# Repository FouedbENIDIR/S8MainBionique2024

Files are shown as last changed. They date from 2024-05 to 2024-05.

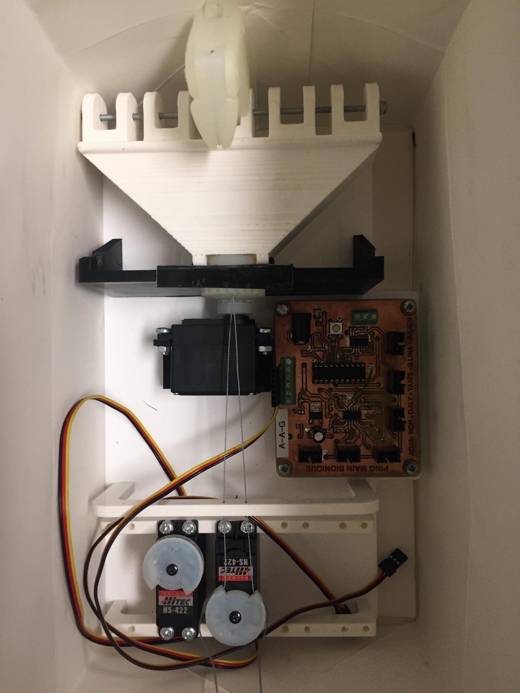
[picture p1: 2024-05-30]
Prototype final.jpeg

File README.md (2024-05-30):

#S8MainBionique2024
Ce répertoire est un recueil des travaux effectués durant le projet S8 2024.

Ce projet, initié il y a quelques années, a pour but de concevoir une main mécanique contrôlée électroniquement par les signaux électriques que le corps envoie au niveau d'un moignon issu d'un bras amputé.

Notre projet S8, après de nombreux problèmes notamment au niveau du code du MSP et de la carte, a été guidé par le désir d'avancer sur la partie mécanique.
Beaucoup de design ont été produit auparavent mais aucun n'est viable et utilisable. En effet la problématique du doigt ayant un pli naturelle a été étudié et plusieurs résultats disponible dans le fichier V2_documentation Mécanique sont indiqués.

DOCUMENT TRES IMPORTANT A LIRE ET A COMPRENDRE AVANT D'AVANCER DANS LE PROJET PARTIE MECANIQUE.

Plusieurs prototypes ont été conçus en répondant aux critères nécessaires énumérés dans le rapport mécanique, présent dans ce répertoire.
"L'utilisation d'une main à 3-4 doigts, avec 2 servomoteurs par doigt, ainsi que l'utilisation de roulements pour fluidifier le mouvement entre chaque phalange doit être étudiée autour d'un projet S8 complet, avec une partie de réflexion autour de nos conclusions, une partie de conception à partir de nos propositions de modèles et une partie de tests permettant de valider ou non le modèle proposé. Si les tests ne sont pas concluants, le groupe reviendra à la conception."

Un projet répondant aux cahier des charges techniques et aux défis encourus peut être un bon moyen de produire une main viable embarquant les servomoteurs mais aussi la batterie.

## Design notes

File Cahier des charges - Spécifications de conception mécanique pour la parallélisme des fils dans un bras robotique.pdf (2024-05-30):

ILINA.K | Date: 08/12/2023
| DOCUMENT TECHNIQIUE : PARTIE MECANIQUE de la main bionique (version 3)
Auteur | Durée de travail
ILINA KHIAT | 12 H
| ➢ Dimanche 26/11/2023 : Rédaction de la
| traçabilité des exigences techniques de la conception mécanique (2H) ➢ Dimanche 03/12/2023 : Continuer la
| Traçabilité des exigences techniques de la conception mécanique (2H) ➢ Jeudi 07/12/2023 : Utilisation du logiciel
| de conception SolidWorks + Rédaction d'une section détaillée décrivant les corrections techniques à apporter lors du processus de conception (3H) ➢ Vendredi 08/12/2023 : Finaliser le cahier des charges + Compléter le Document Principal des Binômes + publier le cahier des charges sur le groupe Teams (5H)

Cahier des charges : conception mécanique

## SPÉCIFICATIONS DE CONCEPTION MÉCANIQUE POUR LE PARALLÉLISME DES FILS DANS UN BRAS

## ROBOTIQUE

Introduction

L'objectif de ce document est de définir les spécifications mécaniques cruciales et les principes nécessaires pour atteindre un parallélisme optimal des fils au niveau des articulations d'un bras robotique pendant les mouvements d'articulation. Les écarts par rapport au parallélisme peuvent entraîner une augmentation des tensions mécaniques dans les tendons, une manœuvrabilité réduite des articulations des doigts et des problèmes potentiels d'enchevêtrement des fils lors de mouvements répétés, ce qui affecte la fonctionnalité globale du bras, sa précision et la durée de vie attendue. Maintenir le parallélisme des fils est une considération importante pour les ingénieurs concepteurs de bras robotiques.

Objectif

L'objectif principal de ce document technique est de définir clairement les spécifications de conception mécanique et les tolérances nécessaires pour concevoir un système de bras robotique qui maintient de manière fiable le parallélisme des fils à chaque articulation pendant les mouvements d'articulation.

Exigences de conception mécanique

La section suivante décrit les principales exigences de conception mécanique à suivre pour garantir que les tendons entre chaque articulation maintiennent un parallélisme adéquat pendant les mouvements d'ouverture et de fermeture de l'articulation.

1. Alignement du Parallélisme des Fils : Les tendons au-dessus et en dessous de chaque articulation doivent être conçus pour maintenir un parallélisme tangentiel lors de l'articulation. Un serrage strict sera nécessaire pendant la phase de conception mécanique.
2. Propriétés du Fil du Tendon : Les tendons doivent être construits avec un fil de haute résistance présentant une élongation élastique minimale sous des charges de tension.
3. Flexibilité du Fil du Tendon : Le matériau du tendon doit permettre un pliage fluide autour d'un rayon minimum de 3 mm sans pliage ni flambage lorsque l'articulation se déplace.
4. Routage Correct des Tendons : Les canaux utilisés pour acheminer les tendons à travers chaque articulation doivent être conçus avec précision pour maintenir une séparation constante des fils et éviter le chevauchement ou l'enchevêtrement pendant le mouvement de l'articulation.
5. Méthode d'Actionnement : Il est recommandé que les mouvements des doigts soient actionnés à l'aide de quatre moteurs servo haute précision de 10g ,4.2 - 6 V pour fournir le couple et le contrôle de position nécessaires pour un mouvement répétable des tendons parallèles.

6. Capacité de Charge : La main robotique devrait pouvoir supporter une masse d'au moins 100 g.
7. Poids : La conception et le matériau devraient donner une structure légère de moins de 300 g.
8. Manipulation d'Objets : Être capable de manipuler des objets couramment utilisés de taille 50 à 100 mm, tels que la manipulation d'objets d'usage quotidien.

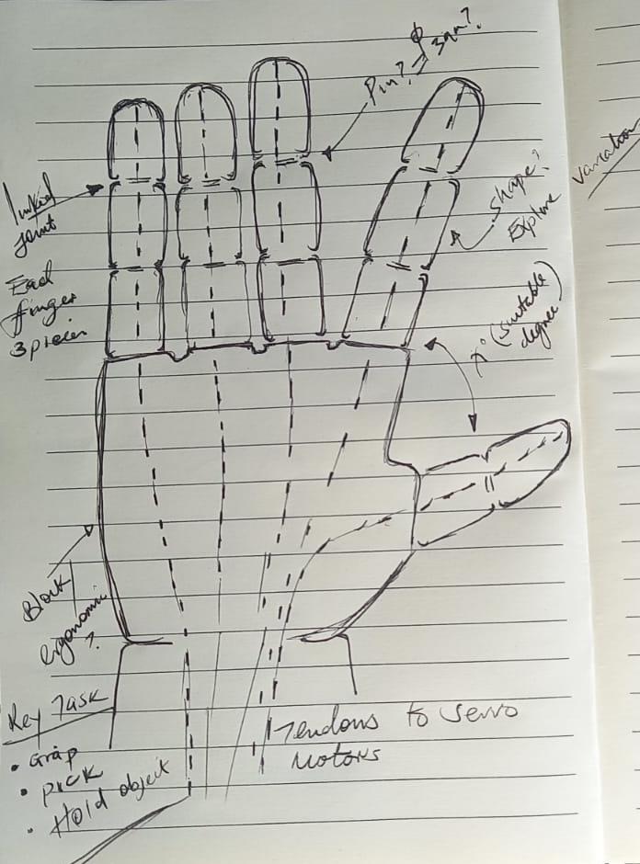
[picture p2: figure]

Figure 1.Croquis préliminaire des principales parties et fonctionnalités du bras.

PARALLÉLISME DES FILS DANS LE MODÈLE "RobHand".

Correction du Parallélisme des Fils.

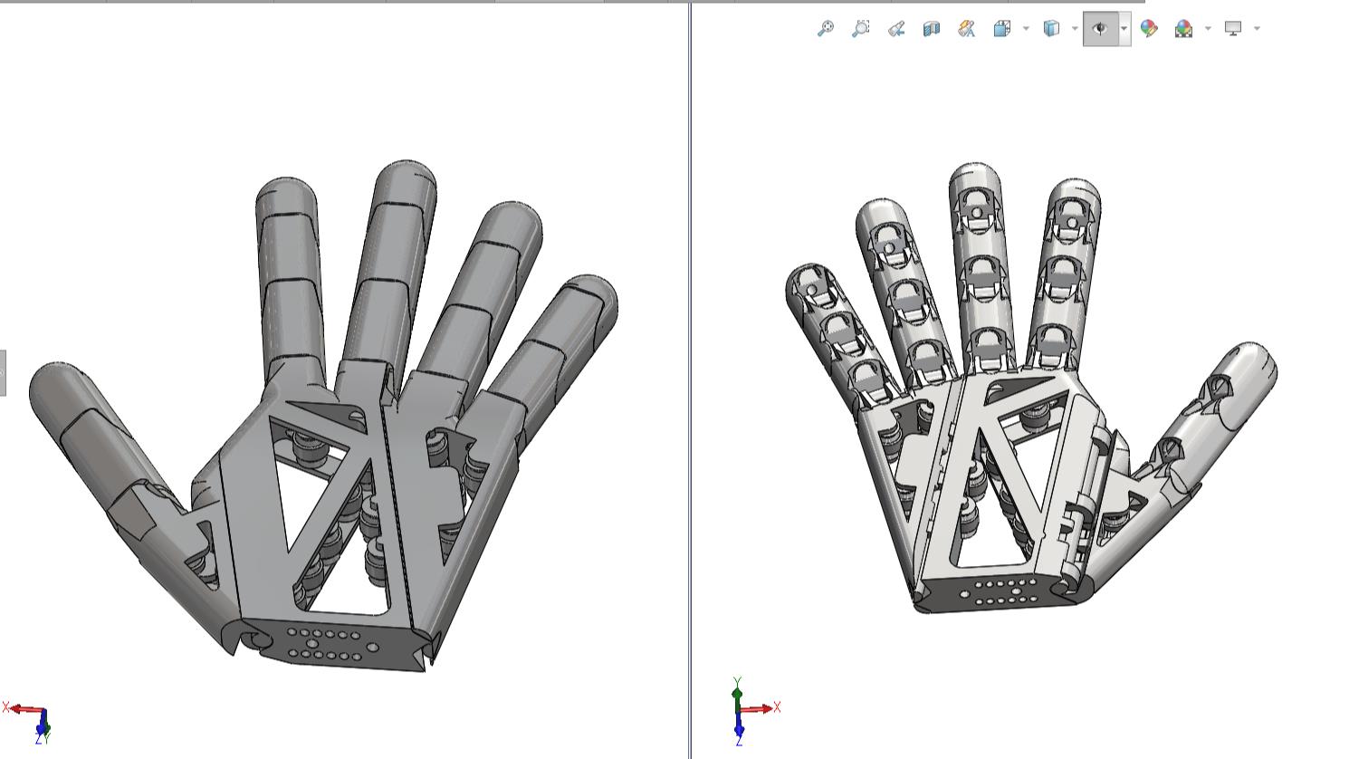
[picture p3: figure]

Figure 2.Capture d'écran du modèle CAO 3D du "RobHand" montrant la vue supérieure et intérieure de la main bionique

À partir du modèle CAO fourni, les fils des tendons au-dessus et en dessous des articulations ne sont pas parallèles lorsque les articulations sont en mouvement, comme illustré dans les images ci-dessous.

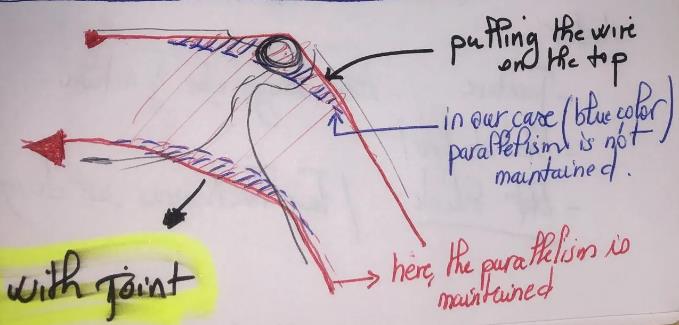
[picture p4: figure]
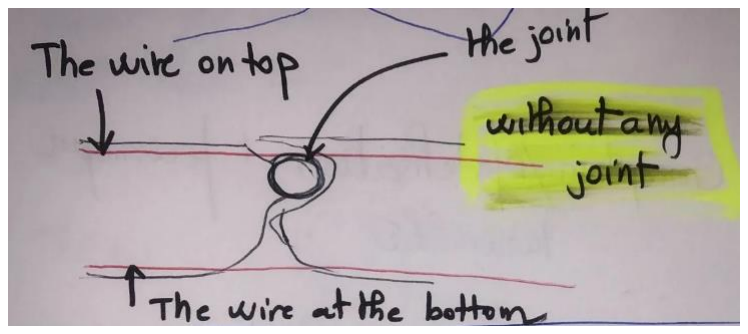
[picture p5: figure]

Figure 3.À droite, articulation d'échantillon en position ouverte. À gauche, articulation d'échantillon montrant un écart de parallélisme.
La procédure de correction de ce modèle impliquera les étapes suivantes :
1. Inspecter le modèle 3D pour identifier comment les sections articulaires spécifiques ont été modélisées.

2. Analyser les trajets de fil existants pour comprendre comment différents paramètres affectent le parallélisme des fils pendant l'articulation.
3. Modifier les angles des articulations et les trajets des fils dans le modèle 3D pour créer un chemin de fil plus lisse et plus parallèle.
4. Utiliser un logiciel de simulation pour visualiser le mouvement des fils pendant l'articulation.
5. Imprimer en 3D une articulation d'échantillon pour tester et itérer en conséquence.

Observations

Une coupe transversale d'un doigt montre que :

- Il y a un routage correct des fils qui garantit qu'il n'y a pas d'enchevêtrement pendant l'articulation.
- Le diamètre maximal autorisé du fil est de 3 mm, mais les chemins le long des doigts ont un espace allant jusqu'à 4,2 mm.
- Le trajet du canal au-dessus de l'articulation du doigt permet au fil du tendon de s'enrouler autour de l'articulation du doigt lorsqu'il se ferme.

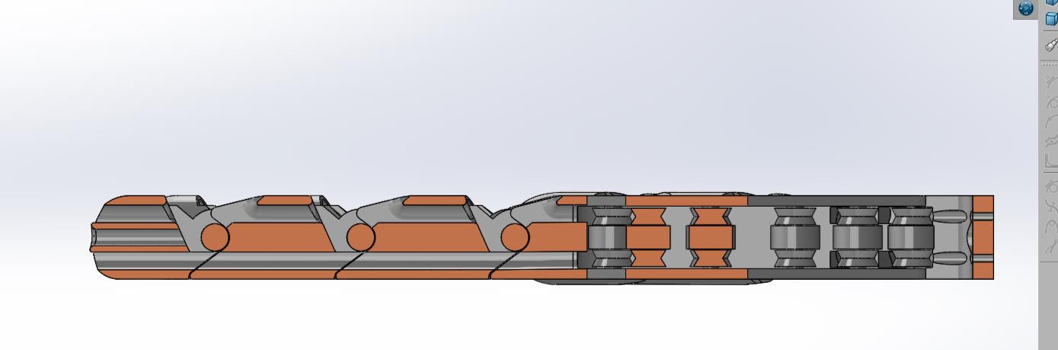
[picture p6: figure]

Figure 4.Vue en coupe d'un doigt et de la paume.
- En analysant le côté intérieur du doigt, on observe que le côté avant des phalanges intermédiaires, des phalanges proximales et de la section des articulations a un écart d'environ ≈ 10 mm par rapport à l'axe de l'articulation. C'est à ce point que le fil du tendon perd son parallélisme.

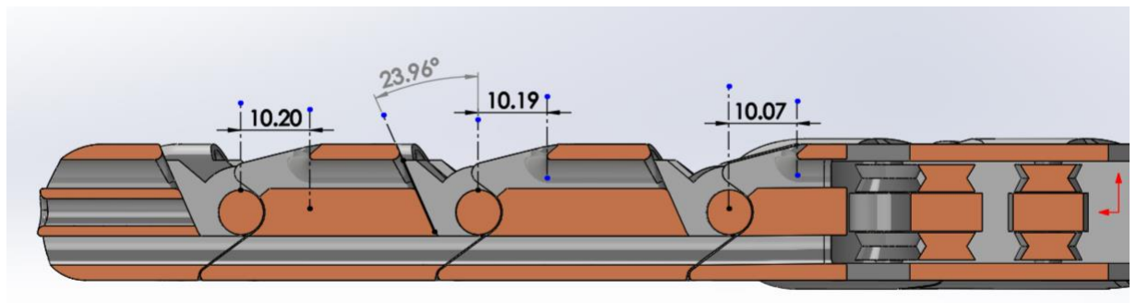
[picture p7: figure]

Figure 5.Décalages de mesure par rapport à l'axe de rotation de l'articulation
- Une inspection minutieuse montre le chemin possible emprunté par le tendon lorsqu'il est tiré.

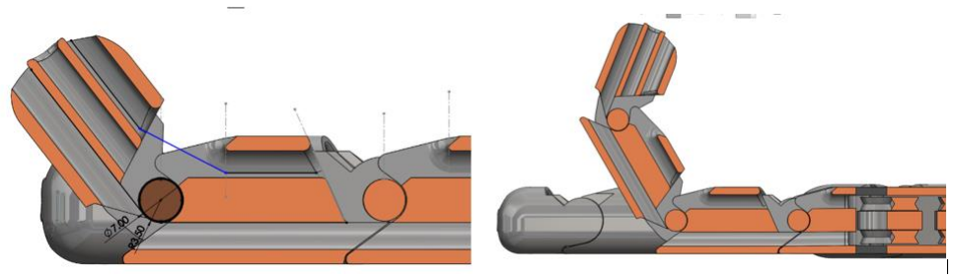
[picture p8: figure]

Figure 6.Différences de flexion des niveaux du doigt d'échantillon.

Ajustements nécessaires

Pour corriger le parallélisme, les phalanges intermédiaires, les phalanges proximales et les points d'articulation seront ajustés par rapport à l'axe de l'articulation afin de maintenir un parallélisme quasi tangentiel entre les tendons supérieur et inférieur.

Calculs mécaniques

Force dans le doigt.

La résistance théorique du doigt, lorsqu'il est complètement ouvert, peut être calculée en analysant les moments créés autour de chaque articulation dans le doigt par ;

Moment = Force x Distance perpendiculaire

M = F x d

Cependant, le moment de l'articulation de l'articulation sera le plus grand, car c'est le plus éloigné et il fournit également la force de rotation qui limite la charge que nous pouvons soulever à l'extrémité du doigt.

Quelle est la force de traction dans le tendon ? Cela sera dérivé par la force de rotation maximale du servo, qui est de 10 kg-cm (1N/M).

Ainsi,

F2 = τServo . d

F2 = 1(N/M) x 10mm

F2 = 10N (Tension dans le Tendon)

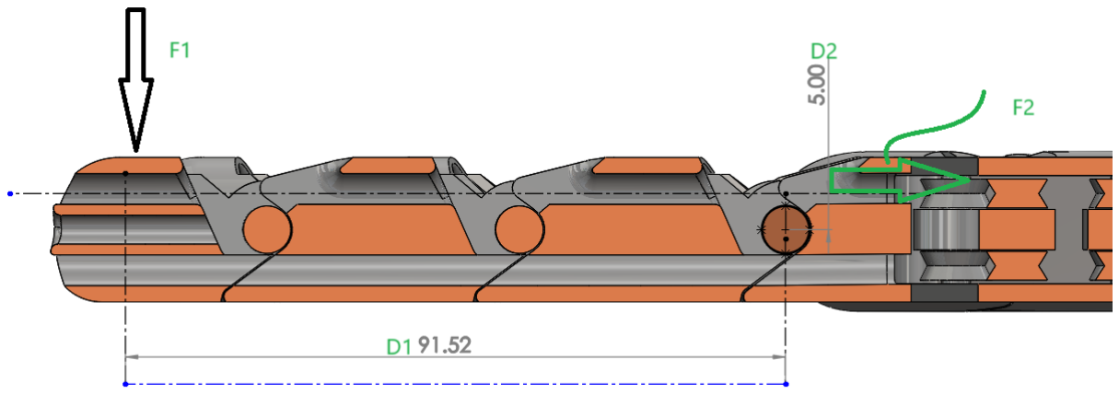
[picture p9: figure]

Figure 7. Forces et distances prises en compte pour les calculs de force.

Ensuite,

F1D1 = F2D2

F1 = (F2D2

)/D1

F1 =

10 x 5
91.52
F1 = 0.55N

Mass 1 ≈ 56.08 g

Cela signifie qu'une force de 0,55N peut être appliquée à chaque doigt lorsqu'il est complètement ouvert. Cependant, lorsque le doigt se replie, le résultat sera un moment moindre autour de l'articulation de l'articulation, et les extrémités appliqueront plus de force à mesure qu'elles se ferment davantage.

Supposons, pendant la flexion, que la distance D 1 = 30 mm, cela permettrait au doigt de supporter environ 163 g, ce qui donnerait une capacité de levage totale du RoboHand d'environ 652 g.

La préℎension maximale de l

′extrémité du doigt ≈ 163g par doigt

Vitesse d'actionnement du doigt

Supposons que notre servo ait une vitesse de fonctionnement de 0,15 s/60⁰. Une rotation complète du poignet d'une position paume vers le haut à une position paume vers le bas (180⁰).

Par conséquent, cela prend (0,15/60) *180 = 0,45 s.

Supposons qu'un tendon se déplace d'environ 2 cm pour déplacer le doigt de complètement ouvert à complètement fléchi.

En utilisant la formule de longueur d'arc

Longueur =

n

0
360⁰ x 2πr

Où la longueur est de 2 cm, r est le rayon des cornes de servo personnalisées (7 mm)

Nous constatons que le servo doit tourner de 160⁰ pour ouvrir/fermer complètement chaque doigt. Cela donne le temps maximal pour ouvrir/fermer un doigt comme (0,15/60) *160 = 0,4 s.

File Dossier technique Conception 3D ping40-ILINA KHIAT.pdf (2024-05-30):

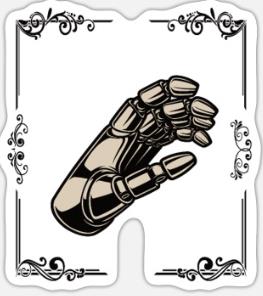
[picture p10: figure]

ILINA KHIAT | Conception mécanique-Prototype de main robotique 2023/2024 | Ping : 40

# DOSSIER TECHNIQUE DE CONCEPTION 3D POUR LE DOIGT ET PROTOTYPE DE MAIN ROBOTIQUE

REALISE PAR : ILINA KHIAT

Introduction.

L'objectif du projet est de concevoir un doigt robotique permettant au fil de tendon de maintenir un parallélisme au sein des phalanges articulaires lors de l'articulation du doigt. Le doigt choisi pour cette conception est le majeur.

CONCEPTION 1

Partie 1. CONCEPTION D'UN SEUL DOIGT ROBOTIQUE

Esquisses de concept

Les esquisses de concept initiales ont été créées en tenant compte des ratios des portions de doigt entre les phalanges distales, intermédiaires et proximales du majeur.

Modélisation 3D

En utilisant SolidWorks, le contour des doigts a été utilisé pour transformer l'esquisse en un modèle 3D détaillé. Cela impliquait l'utilisation des fonctionnalités de SolidWorks telles que les esquisses, les images d'esquisses, les extrusions, les révolutions et les lofts. Un modèle maître à plusieurs corps du doigt a été conçu, servant de base pour les étapes ultérieures de perfectionnement du design.

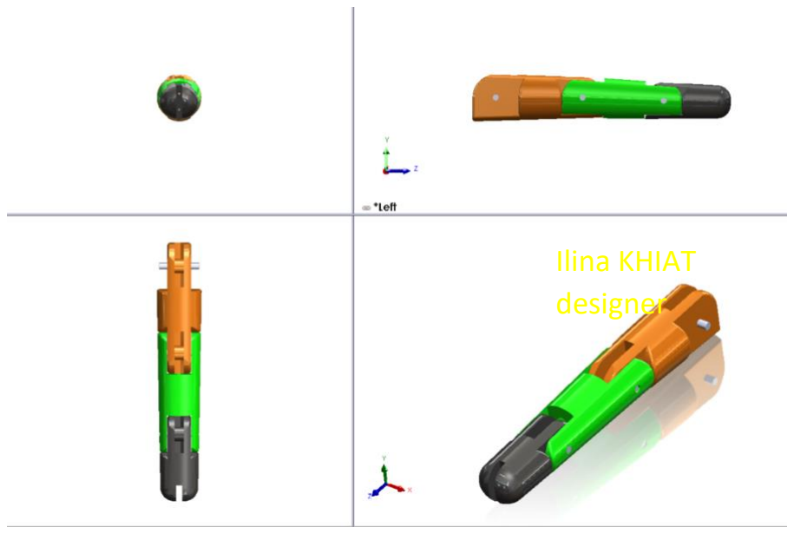
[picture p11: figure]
Ilina KHIAT designer

Figure 2. Vue en première angle du doigt conçu

Pendant le processus de modélisation, une attention particulière a été accordée pour s'assurer que les parties du doigt permettaient au fil de tendon de passer à travers les différentes articulations du doigt tout en maintenant le parallélisme.

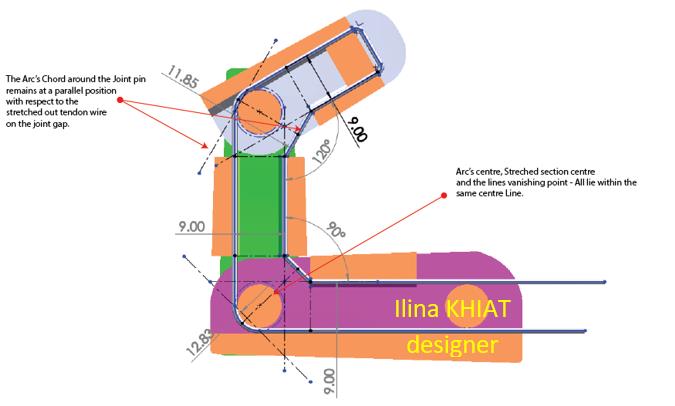
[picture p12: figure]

Figure 3. Vue en coupe du doigt montrant les dimensions pour le parallélisme du tendon.

Assemblage et Simulation

À partir de la partie à plusieurs corps, des parties individuelles des phalanges du doigt ont été créées en utilisant la commande " save body ".

Figure 4. Modèles dérivés des phalanges proximale, intermédiaire, distale et de la broche d'articulation du doigt

Les parties du doigt ont ensuite été importées dans l'environnement d'assemblage de SolidWorks et assemblées à l'aide de liaisons appropriées telles que les liaisons articulées, concentriques, de largeur, coïncidentes et de limitation. Ces liaisons ont permis l'étude du mouvement du doigt.

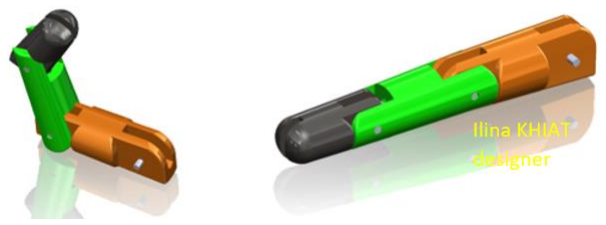
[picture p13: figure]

Figure 5. Assembler le doigt.

Après la création de l'assemblage, une analyse de mouvement avec SolidWorks a été utilisée pour examiner comment les phalanges du doigt s'articulent tout en maintenant le parallélisme requis du fil de tendon autour des points d'articulation.

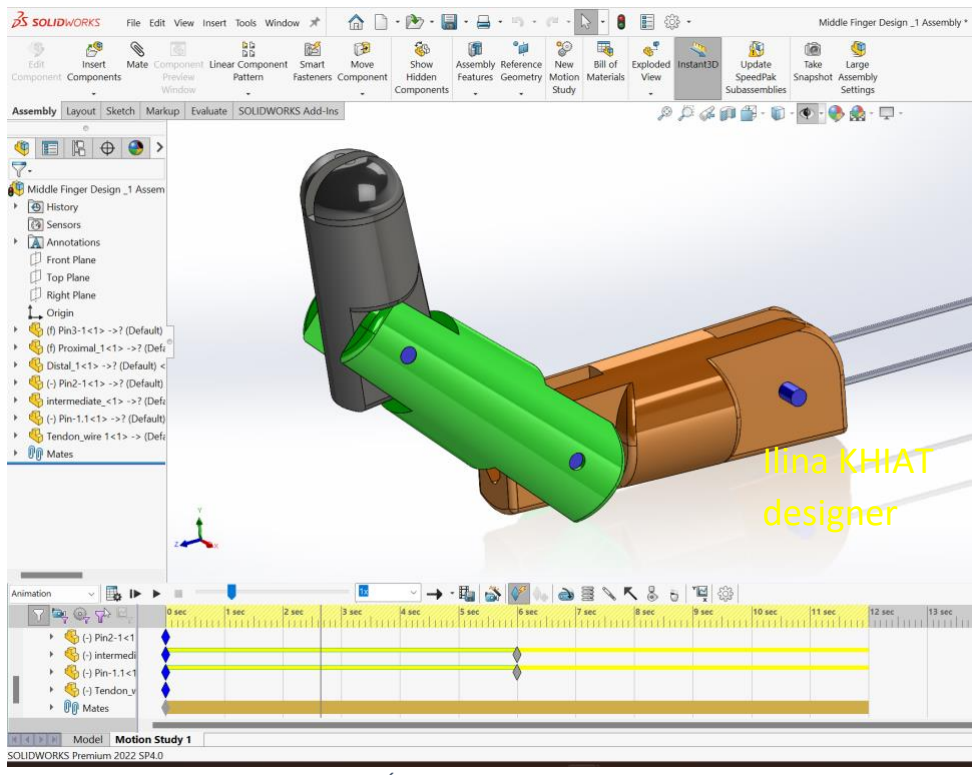
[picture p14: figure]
Ilina KHIAT designer

Figure 6.Étude de mouvement du doigt

Le comportement cinématique d'un assemblage, dans le contexte de SolidWorks, se réfère à la manière dont les composants interagissent et se déplacent les uns par rapport aux autres. Pour examiner le mouvement des fils au niveau des phalanges du doigt, j’ai utilisé l'option "SolidWorks Motion Analysis". Cette fonctionnalité permet de simuler et de suivre le mouvement des composants individuels, comme les fils dans le cas des phalanges du doigt. Comme le montre la configuration en haut, le parallélisme des fils est maintenu pendant l'articulation du doigt. Cela peut être une étape importante pour valider la conception et optimiser le mécanisme du doigt dans le modèle 3D.

Figure 7.Dessin technique de conception d'un doigt robotique 1

CONCEPTION 2

Partie 1. CONCEPTION D'UN SEUL DOIGT ROBOTIQUE

Esquisses de concept

Les esquisses de concept initiales ont été créées en tenant compte des ratios des portions de doigt entre les phalanges distales, intermédiaires et proximales du majeur.

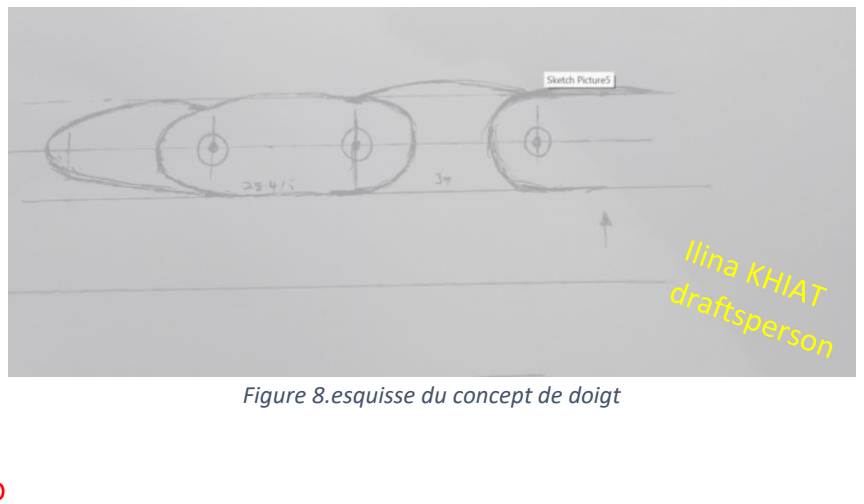
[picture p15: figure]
Figure 8.esquisse du concept de doigt

Modélisation 3D

En utilisant SolidWorks, le contour des doigts a été utilisé pour transformer l'esquisse en un modèle 3D détaillé. Cela impliquait l'utilisation des fonctionnalités de SolidWorks telles que les esquisses, les images d'esquisses, les extrusions, les révolutions et les lofts. Un modèle principal à plusieurs corps du doigt a été conçu, servant de base pour les étapes ultérieures de perfectionnement du design.

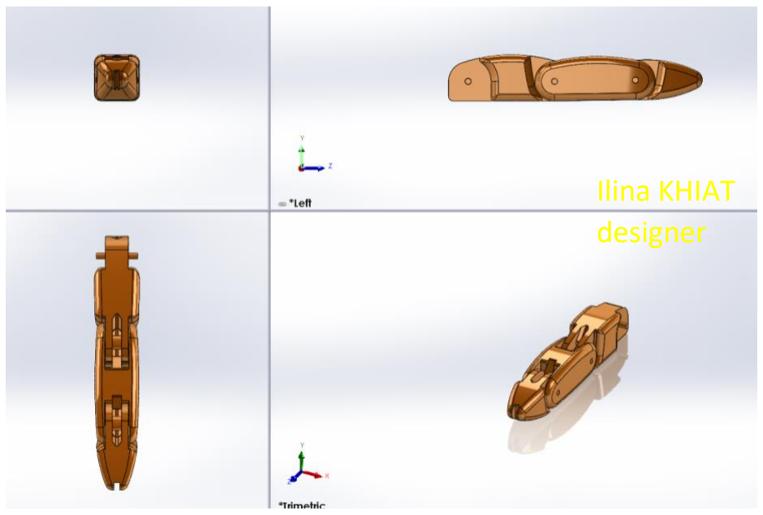
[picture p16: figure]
Ilina KHIAT designer

Figure 9. Vue en première angle du doigt conçu

Pendant le processus de modélisation, une attention particulière a été accordée pour s'assurer que les parties du doigt permettaient au fil de tendon de passer à travers les différentes articulations du doigt tout en maintenant le parallélisme.

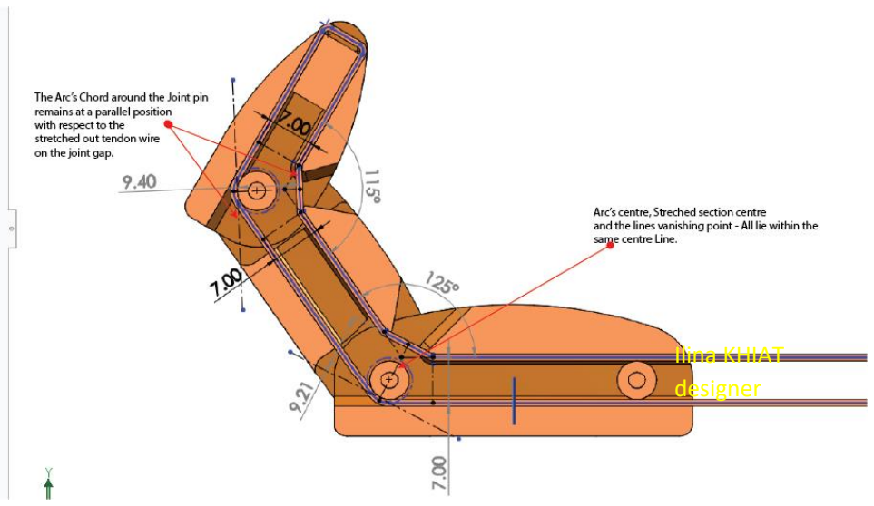
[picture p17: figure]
Ilina KHIAT designer

Figure 10. Vue en coupe du doigt montrant les dimensions pour le parallélisme du tendon.

Assemblage et Simulation

À partir de la partie à plusieurs corps, des parties individuelles des phalanges du doigt ont été créées en utilisant la commande " save body ".

Figure 10. Modèles dérivés des phalanges proximale, intermédiaire, distale et de la broche d'articulation du doigt

Les parties du doigt ont ensuite été importées dans l'environnement d'assemblage de SolidWorks et assemblées à l'aide de liaisons appropriées d’assemblage telles que les liaisons articulées, concentriques, de largeur, coïncidentes et de limitation. Ces liaisons ont permis l'étude du
mouvement du doigt.

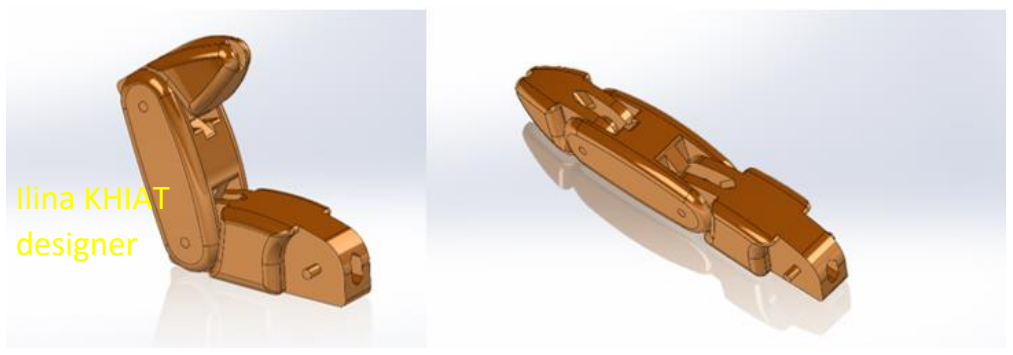
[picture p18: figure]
Ilina KHIAT designer

Figure 11. Assembler le doigt.

Après la création de l'assemblage, une analyse de mouvement avec SolidWorks a été utilisée pour examiner comment les phalanges du doigt s'articulent tout en maintenant le parallélisme requis du fil de tendon autour des points d'articulation.

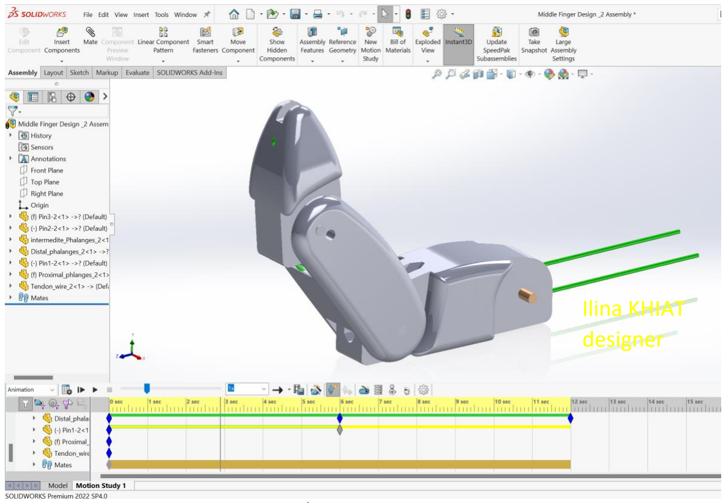
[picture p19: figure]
Ilina KHIAT designer

Figure 12.Étude de mouvement du doigt

Figure 13.Dessin technique de conception d'un doigt robotique 2

CONCEPTION 3

Partie 1. CONCEPTION D'UN SEUL DOIGT ROBOTIQUE

Esquisses de concept

Les esquisses de concept initiales ont été créées en tenant compte des ratios des portions de doigt entre les phalanges distales, intermédiaires et proximales du majeur.

Modélisation 3D

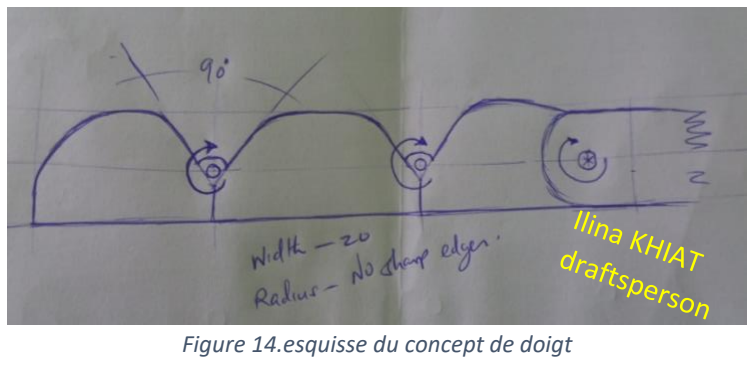
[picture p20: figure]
Figure 14.esquisse du concept de doigt

En utilisant SolidWorks, le contour des doigts a été utilisé pour transformer l'esquisse en un modèle 3D détaillé. Cela impliquait l'utilisation des fonctionnalités de SolidWorks telles que les esquisses, les images d'esquisses, les extrusions, les révolutions et les lofts. Un modèle principal à plusieurs corps du doigt a été conçu, servant de base pour les étapes ultérieures de perfectionnement du design.

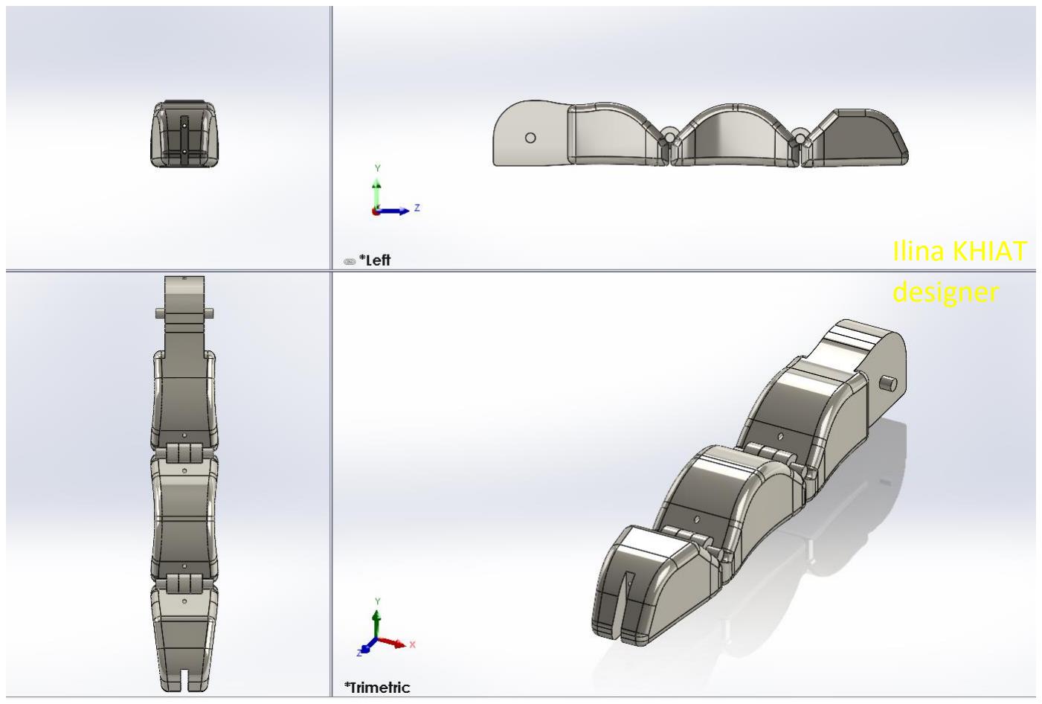
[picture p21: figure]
Ilina KHIAT designer

Figure 15.Vue en première angle du doigt conçu

Pendant le processus de modélisation, une attention particulière a été accordée pour s'assurer que les parties du doigt permettaient au fil de tendon de passer à travers les différentes articulations du doigt tout en maintenant le parallélisme.

Figure 16. Vue en coupe du doigt montrant les dimensions pour le parallélisme du tendon.

Assemblage et Simulation

À partir de la partie à plusieurs corps, des parties individuelles des phalanges du doigt ont été créées en utilisant la commande " save body ".

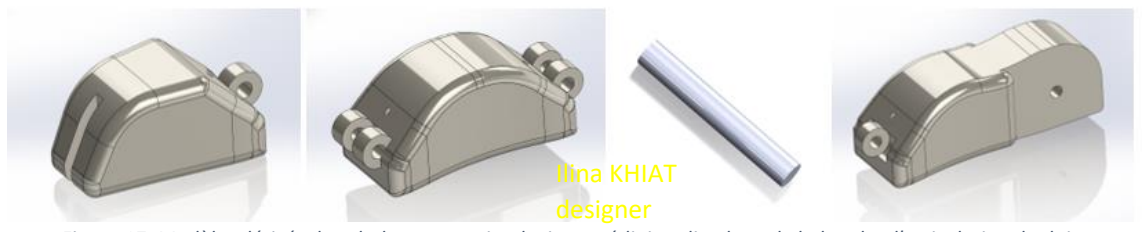
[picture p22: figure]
Ilina KHIAT designer

Figure 17. Modèles dérivés des phalanges proximale, intermédiaire, distale et de la broche d'articulation du doigt

Les parties du doigt ont ensuite été importées dans l'environnement d'assemblage de SolidWorks et assemblées à l'aide de liaisons appropriées d’assemblage telles que les liaisons articulées, concentriques, de largeur, coïncidentes et de limitation. Ces liaisons ont permis l'étude du mouvement du doigt.

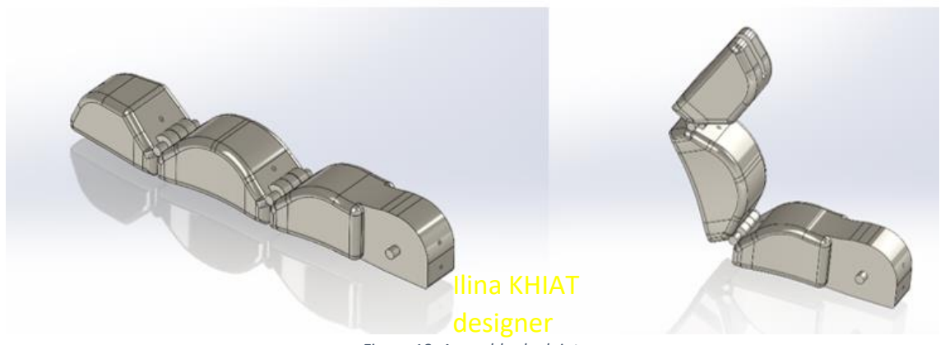
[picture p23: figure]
Ilina KHIAT designer

Figure 18. Assembler le doigt.

Après la création de l'assemblage, une analyse de mouvement avec SolidWorks a été utilisée pour examiner comment les phalanges du doigt s'articulent tout en maintenant le parallélisme requis du fil de tendon autour des points d'articulation.

Figure 19.Étude de mouvement du doigt

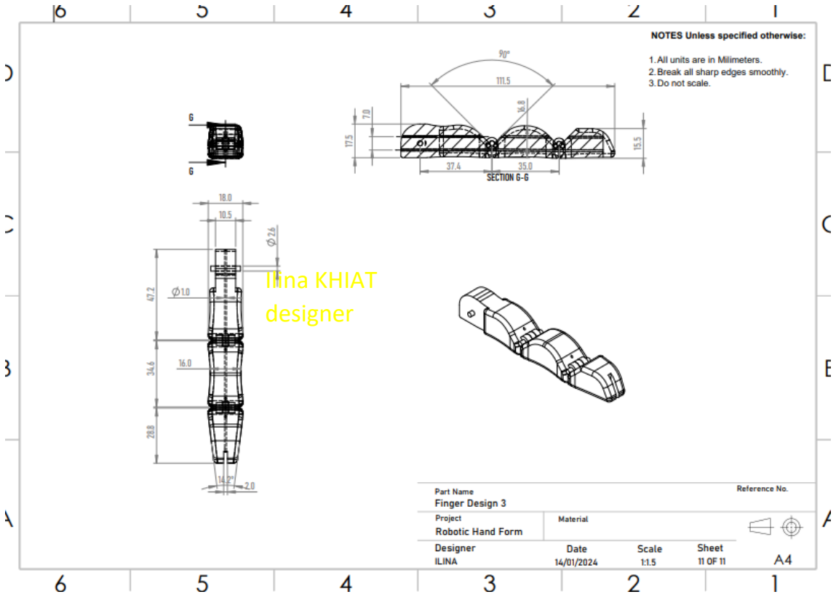
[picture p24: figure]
Ilina KHIAT designer

Figure 20.Dessin technique de conception d'un doigt robotique 3

b. Introduction.

La prochaine phase du projet visait à créer une "main robotique" avec 6 doigts actionnés par 6 servomoteurs, capable d'effectuer un mouvement de supination. La structure du modèle était guidée par le modèle illustré.

Note : Une modification a été apportée après la conception de ces trois prototypes de main

robotique. La modification consistait à supprimer un doigt (le sixième) et à ajuster les trois prototypes déjà conçus avec tous les éléments des maquettes.

Partie 2. CONCEPTION DU PROTYPE DE LA MAIN ROBOTIQUE

Pour comprendre la conception du prototype à réaliser, je me suis basée sur un dessin ci-dessous illustrant l'idée.

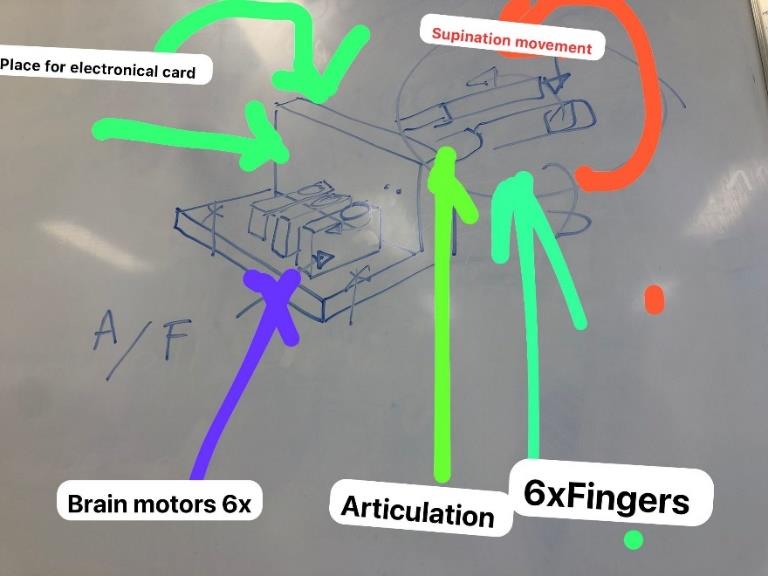
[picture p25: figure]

Figure 21. esquisse du "prototype de main robotique".

Le modèle du servomoteur à utiliser était le servomoteur Deluxe HS-422, avec ses dimensions telles qu'indiquées dans le diagramme ci-dessous.

Figure 22.Datasheet des servomoteurs DELUXE HS-422

Disposition des composants.

En tenant compte du croquis, de la taille du servomoteur et des dimensions des doigts, un plan pour connecter les composants au sein d'une base a été développé en utilisant une esquisse dimensionnée de SolidWorks.

Ilina KHIAT designer

Figure 23.Esquisse de la disposition des composants.

c. Forme du métacarpe

Avec les composants disposés, un modèle 3D détaillé du métacarpe a été conçu pour accueillir les six doigts. La section interne a été évidée pour permettre le passage des fils de tendon et réduire le poids.


Figure 24 : Modèle du métacarpe

La forme métacarpienne est connectée au mécanisme de supination à l'aide d'une vis M3.

d. Engrenages de supination.

Pour permettre le mouvement de supination, des engrenages imprimés en 3D, reliés à un servomoteur, sont conçus et intégrés. Ces engrenages se composent d'un engrenage conducteur avec 11 dents et d'un engrenage mené avec 20 dents.

Figure 25. Engrenages de supination

L'engrenage mené comporte une série de trous à travers lesquels passent les fils de tendon pour éviter tout emmêlement pendant le mouvement.

e. Guide des fils de tendon.

Pour organiser davantage les fils de tendon, un guide vertical avec des trous a été conçu pour garantir que les fils provenant de l'engrenage mené de supination sont sur un plan horizontal plat lorsqu'ils entrent dans les poulies du servomoteur.

Ilina KHIAT designer

Figure 26. Guide des fils de tendon.

f. Poulies de servomoteur.

Connectées aux servomoteurs, les poulies maintiennent les extrémités des fils de tendon au-dessus et en dessous de chaque doigt. Elles facilitent l'articulation des doigts lorsqu'elles sont actionnées par les servomoteurs, soit en tirant, soit en relâchant les fils de tendon.

Figure 27.Poulies de servomoteur.
g. Supports de servomoteur.

Les supports de servomoteur sont également conçus pour permettre aux moteurs d'être fixés par une vis M4.

Figure 28.Supports de servomoteurs h. Base de la forme de main robotique

Tous les composants de la forme de main sont supportés par une base de taille 138 x 250 mm et maintenus ensemble à l'aide de vis M4 x 12 mm à tête fraisée (CSK) depuis le bas de la plaque de base.

Ilina KHIAT designer

Figure 29.Plaque de base.

Assemblage de la "forme de main robotique"

Après la conception de toutes les pièces, la "forme de main robotique" a été assemblée en utilisant des éléments appropriés et en incorporant des moteurs de taille précise pour une visualisation précise du modèle.

Ilina KHIAT designer

Figure 30.Images montrant la "forme de main robotique" assemblée en première projection angulaire, en vue 3D isométrique et en vue éclatée (design doigt 2).

Analyse de la prise de la forme de main robotique

Pour vérifier la capacité de préhension de la main, une boule sphérique a été modélisée et assemblée avec les doigts afin d'évaluer sa capacité de préhension et de maintien.

Figure 31."Forme de main robotique», design doigt 2 saisissant une boule sphérique.

Figure 32."Forme de main robotique», design doigt 1, saisissant une boule sphérique.

Ilina KHIAT
designer

Ilina KHIAT
designer

Ilina KHIAT designer

Figure 33."Forme de main robotique», design doigt 3, saisissant une boule sphérique.

Impression 3D / Assemblage et montage du prototype :

La tolérance de 0,5 mm de l'imprimante 3D a été prise en considération lors de l'impression 3D de tous les composants mécaniques du prototype (doigts, supports …) de la main bionique, en utilisant une impression à résine. Des ajustements ont été apportés en cas de contraintes d'impression. Ensuite, un assemblage des 5 designs des doigts imprimés a été fait et le montage de tous les composants du prototype de la main bionique a été assemblé sur la plaque de base ((métacarpe, engrenage de supination, les servomoteurs, les poulies, les fils, les Guides de fil de tendon, la PCB sur la base).


Figure 34.Impressions 3D des différents designs de doigts

Figure 35.Impression 3D et montage du prototype de main robotique

Réalisation des tests mécaniques post-impression 3D et test du mouvement du doigt au laboratoire:

1-Test de flexibilité et de mobilité : Évaluer la souplesse des articulations des doigts.
2-Test de résistance des matériaux : Appliquer des charges variables pour évaluer la solidité et la résistance des matériaux utilisés sans déformation ni rupture. 3-Test du parallélisme des fils :
-Inspection visuelle : Vérifier l'alignement des fils en haut et en bas des doigts en position neutre.
-Test de traction : Appliquer une tension aux fils pour s'assurer qu'ils restent parallèles lorsqu'ils sont soumis à différentes forces.
4-Test de rotation des engrenages : Évaluer la fluidité et l'efficacité de la rotation des engrenages pour transmettre le mouvement.
5-Test du passage des fils sans friction :
-Test de glissement des fils : Évaluer la facilité de déplacement des fils à travers les trous sans générer de friction excessive.
6-Test de rotation du métacarpe manuellement : Vérification de la rotation à 45 degrés.
7-Utilisation d'un testeur servomoteur pour actionner le moteur et effectuer le mouvement des doigts en essayant plusieurs câblages des fils.


Figure 36.Actionner le servomoteur pour effectuer le mouvement des doigts.

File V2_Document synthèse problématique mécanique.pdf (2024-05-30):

Document synthèse problématique mécanique

Projet S8 « Main Bionique »

La conception de la main bionique a été étoffé au fil des projets qui se sont succédés sur le sujet.

Beaucoup de bons points ont été réalisé mais également beaucoup de problématiques reste à résoudre.

Nous allons voir dans ce document les différentes versions avec les bons points, les mauvais points et ce que l’on peut garder pour la version finale.

Dans ce document P1 correspond à la phalange 1 du doigt et naturellement P2 et P3 aux phalanges 2 et 3.

Sommaire :

1- Résultats des prototypes des années précédentes
2- Analyse personnelle des précédentes prototypes et proposition de résolution envisagée 3- Synthèse d’analyse sous forme de tableau


1 – Résultats des années précédentes

Ping 2023

Cette année-là le groupe de PING s’est penché concrètement sur la problématique mécanique avec un vrai travail d’analyse des forces applicables sur chaque membre, en proposant une amélioration d’un prototype précédent. Le cahier des charges de leur groupe était le suivant :


En effet les résultats de leur analyse sont les suivants :

Concernant le prototype proposé par ce groupe, nous pouvons constater qu’en contraction, le doigts se plie phalange par phalange et nous avons du mou au niveau de l’extrémité du fil, pouvant laisser penser à un déchaussement futur.

2 - Analyse personnelle des précédentes prototypes et proposition de résolution envisagée

Les premiers prototypes se sont confrontés aux problèmes suivants :

Problème de solidité : On a pu constater qu’au bout de quelques manipulations, les jointures se cassaient rapidement. Un vrai travail de mouvement et de résistance doit être effectuer en amont, comme avec un test d’effort sur Solidworks.

Solution Proposé : Se concentrer sur les jointures pour avoir des mouvements fluides et plus solides. L’utilisation de roulements peut permettre d’éviter les frottements entre chaque phalange. L’utilisation de liaison pivot avec un panel d’angle définis entre chaque phalange est aussi à étudier.

Pour une éventuelle partie commerciale, des matériaux plus résistants ( tel que du carbone ou du titane) aux efforts constant devront être envisagé à l’avenir. Pour l’instant des modèles en polymère sont suffisants.

Problème anatomique : L’anatomie d’une main et les fonctions biomécaniques des doigts doivent se dérouler de la manière suivante comme décrite dans la vidéo : https://youtu.be/n17IYU0G6cI?feature=shared

On voit dans la vidéo qu’un déroulé des phalanges P1 à P3 doit se faire circulaire et non linéaire : les phalanges doivent se plier sous la traction du servomoteur tous en même temps et non chacun leur tour. (Problème constaté sur TOUS les prototypes déjà réalisés, cette problématique n’a toujours pas été résolu).

Solution proposée : Effectuer un vrai travail anatomique de la main en prenant en compte la contrainte des servomoteurs utilisables (nous en avons 6 à disposition). Joindre l’index avec le majeur ainsi que l’auriculaire avec l’annulaire peut résoudre la problématique du nombre de servomoteurs utilisables. De plus la main doit être scindée en 2 avec une face bombée et l’autre plus creuse correspondant à la paume de celle-ci, permettant d’attraper les objets de matière plus facilement qu’une surface plane. Ce modèle est à conserver en l’améliorant.

Donc partir sur un modèle à 3 doigts pilotés par 2 servomoteurs chacun est envisageable.

Problème du Pouce : Le pouce est un ensemble de phalange entouré par des muscles permettant le déplacement selon plusieurs axes de mouvements : Flexion et extension, Rotation autour de sa base (circumduction), Abduction et adduction permettant l'opposition aux autres doigts longs de la main.


La contrainte est que le pouce possède une multitude d’axe de mouvement. Ce problème a été pris en compte sur certain prototype comme sur celui-ci :

Cependant comme nous pouvons le constater, l’abduction et l’adduction ne sont ni assez profonde ni dans le bon sens pour permettre de maintenir une position ronde.

De plus en considérant le fait d’utiliser seulement 2 servomoteurs pour le pouce, nous devons donc exclure certains axes de mouvement.

Solution : L’abduction ainsi que l’adduction semble être des éléments clés pour prendre en main un objet. Une liaison selle pour P1 et P2 ainsi qu’une liaison ellipsoïde contraint à l’extension et la flexion entre P2 et P3 peut être une solution. La première liaison serait commandé par un servomoteur et la seconde par un autre.


Partir d’une position mécanique de base plus ronde de la main permettrait de se passer des mouvements d’antéposition et de rétroposition, permettant à notre pouce d’effectuer une flexion/extension, abduction/adduction ainsi que des mouvements couplant certains mouvements ensemble comme l’opposition du pouce et du doigts.

Problème de tirage des câbles, fermeture naturelle.

L’un des problèmes majeurs non résolus reste la flexion et l’extension naturelle des doigts. Jusqu’à présent, un servomoteur était utilisé par doigts en se focalisant sur 5 doigts. Anatomiquement les doigts sont composés d’une multitude de tendons et de muscles permettant de maintenir en place le tout. L’utilisation d’élastique, à l’image de tendon qui possède également une certaine élasticité est à conserver. L’utilisation de roulements dans les jointures fluidifiant les mouvements en limitant les frottements, couplé au guidage des élastiques pourrait corriger la flexion en la guidant.

Reste maintenant l’extension. Aucun groupe n’a jusqu’à l’heure proposé de solutions convaincantes. Le problème observé sur tous les prototypes est le déroulé P3-P2-P1 lors d’une flexion, et pas d’extension convaincante.

L’utilisation des 2 servomoteurs, l’un relié à P2 et l’autre à P3, avec un tirage commun assisté par les élastiques pourrait être une solution. En effet, si l’on tire P2 et P3 en même temps nous pourrons avoir un déroulé plus naturel. Une architecture plus enclin à se plier pour P1 est à prévoir.

Pourquoi les servomoteurs sont placés sur P2 et P3 ?

Selon plusieurs études se concentrant sur la répartition des forces de pincement sur les doigts
(cf. « The Biomechanics of Grasping and Manipulation » Source: Journal of Biomechanics, ou encore « The Role of Thumb and Fingers in Grasping A Biomechanical Analysis » paru dans Clinical Biomechanics)

3-Récapitulatif sous forme de tableau des problèmes rencontrés, de l’explication et d’une proposition de solution envisagé.

Problème | Explication | Solution proposée
Solidité | Besoin de solidité qui ne doit pas être (ou du moins le moins possible) frotté aux parois pour éviter une dégradation rapide | Cable de dérailleur (vélo) 1,2mm + gaine 1mm
Longueur des fils | Eviter un mou lors d’une extension | Tendu au maximum
Pouce Opposable | Cf anatomie du pouce | Articulation en selle + articulation ellipsoïdale
Matériaux | Aspect seulement mécanique pour l’instant. | Polymère et résine pour le moment, puis matériaux + résistant
Dimensions | | Dimension d’une main classique d’un adulte

Intégration
Plie des doigts | Cf explications | Flexion + extension réaliser par l’action commune de 2 servomoteurs
Pilotage des servomoteurs | | Commandé par le nerf médian ou le moignon (point non résolu)

Interface
Symétrie Droite/gauche | Application à but commercial sans distinction | Faire 2 versions

Sources :

Pour la justifications des phalanges :

The Biomechanics of Grasping and Manipulation

https://academic.oup.com/biolinnean/article/127/3/535/5521438?login=false

Original Source: Journal of Biomechanics

Measurement of Pinch and Grip Strength in Upper Extremity

https://www.ncbi.nlm.nih.gov/pmc/articles/PMC5123260/

Original Source: Journal of Rehabilitation Research and Development

Livres pour aller plus loin :

Anatomy and Human Movement: Structure and Function, Authors: Nigel Palastanga, Roger Soames

Kinesiology of the Musculoskeletal System, Author: Donald A. Neumann

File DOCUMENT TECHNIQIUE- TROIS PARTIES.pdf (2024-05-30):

DOCUMENT TECHNIQIUE : PARTIE MECANIQUE de la main bionique (version 3)

Les parties du document technique :

1- Génralite : anatomie de la main / doigts / articulations
2- Description de l’evolution de la conception mecanique de la main 3- Problématique mécanique, Impacts
4- Cahier des charges et solutions technique envisageables

Document rédigé :
17/11/2023

Auteur :
ILINA KHIAT

Durée de travail :

Jeudi : 16/11/2023 : Documentation, compréhension de la problématique (5H)

Vendredi : 17/11/2023 : rédaction du document (4H)

PARTIE GENERALITE :

1- La main :

La main humaine comprend une large paume et 5 doigts. Elle est attachée au reste du corps par une liaison appelée le poignet. Le dos de la main se nomme dorsum et le côté intérieur de la main est désigné comme étant la paume.

La paume est bordée latéralement par deux éminences ou saillies convexes : l’éminence thénar, sous le pouce et l’éminence hypothénar. La paume comporte trois rides profondes, présentes dès la naissance et un pli généralement présent :

- le pli palmaire inférieur ;
- le pli palmaire moyen ;
- le pli palmaire supérieur ;
- le pli hypothénarien ;


Figure 1– La main humaine

2- Les doigts

Les cinq doigts de la mains sont (figure 3):

- le pouce (D1) ;
- l’index (D2) ;
- le majeur (D3) ;
- l’annulaire (D4) ;
- l’auriculaire (D5) ;

2-1 Les articulations au niveau des phalanges

La main comporte les articulations suivantes :

A- Articulations au niveau des phalanges, responsables du mouvement du doigt :

- les liaisons inter-phalangiennes (IP, IPP et IPD) ;


B- Articulations au niveau de la paume de la main, permettant de réaliser des mouvements et des gestes complexes avec la main, dont sa fermeture en forme de poing

- la liaison radio-carpienne
- les liaisons inter-carpiennes ;
- les liaisons carpo-métacarpiennes ;
- les liaisons inter-métacarpiennees ;
- les liaisons métacarpo-phalangiennes (MCP) ;

Deux phalanges composent le pouce, notées P1 et P3 (voir figure 2). Trois phalanges composent chacun des autres doigts, notés P1, P2 et P3. Elles sont également connues, dans l’ordre, sous les noms de phalange proximale, phalange médiane et phalange distale. Très innervée, la phalange distale, comprenant l’ongle, possède une grande sensibilité et permet à l’humain de mieux ressentir son environnement (chaud, froid, textures, etc.)


Figure 2 : Visualisation des articulations au niveau des quatorzes phalanges.


Figure 3 – Notation de la main (source : CSSS d’Arthabaska-et-de-l’Érable)
PARTIE 1 : État de l'art actuel de la main bionique (version 3)

Description technique de la main bionique (Version 3) :

La main bionique, conçue à l'aide du logiciel Fusion 360, présente une architecture avancée de trois phalanges par doigt, chacune équipée de trois articulations, à l'exception du pouce. Cette configuration offre une grande variété de mouvements, allant de la préhension à l'ouverture et la fermeture, reproduisant de manière réaliste la fonctionnalité de la main humaine. Deux plis spécifiques : extension/flexion du pouce, et un pli de deux doigts : D4 et D5 , ces articulations sont intégrées au niveau de la paume, renforçant ainsi la polyvalence et la dextérité de la prothèse.


Évolution de la conception d'une main bionique :

- Première version :
- Composition : Main en matériaux plastiques.
- Doigt unique avec 3 phalanges et 3 articulations.
- Paume sans articulation à l'épaule de la main.


- Deuxième version :
- Structure : Avant-bras intégré dans un boîtier cylindrique en plastique.
- Main avec impression en poudre, dotée de 5 doigts.
- Une seule articulation au niveau de la paume de la main, matériaux : polymères


- Troisième version :
Caractéristiques :
- Partie main et 5 doigts avec 4 articulations (IP, IPP et IPD) et 3 phalanges et, exception faite du pouce avec deux phalanges et deux articulations.
- Impression en poudre via une imprimante 3D.
- La paume de la main dispose de deux articulations.
- Partie avant-bras avec impression 3D en poudre.
Système de contrôle :
- Trois cerveaux moteurs (3/3) sur le coude de l'avant-bras.
- Contrôle des articulations et des mouvements des phalanges.
- Gestion des fils entourant ces phalanges.


Le problématique mécanique à résoudre :

L'incohérence mécanique observée lors de la création d'articulations réside dans le fait que les fils supérieurs et inférieurs qui entourent chaque doigt ne restent pas parallèles pendant l'articulation. Cela découle d'une déviation dans la trajectoire des fils lorsqu'ils sont sollicités, , ainsi les arcs des fils ne partagent pas le même centre d'arc. Cette déviation est particulièrement accentuée lors de la sollicitation des fils supérieurs ou inferieurs pour initier une articulation, entraînant un impact significatif sur la mécanique globale.

Le défi principal de la conception mécanique réside dans le non-parallélisme des fils supérieurs et inférieurs de chaque doigt lors de la création d'articulations. Lorsqu'on tire les fils du haut, les deux fils, supérieurs et inférieurs, ne restent pas parallèles, résultant d'une déviation dans la trajectoire des fils lorsqu'ils sont sollicités. Ce problème est particulièrement accentué lors de la création de l'articulation.


Illustration : Représentation schématique du défi mécanique à résoudre.

Impact sur les Articulations des Phalanges :

1- Contraintes Inégales :
La différence des trajectoires peut entraîner des contraintes inégales sur les articulations, ce qui peut causer des problèmes tels que l'usure prématurée ou la défaillance des composants des phalanges.
2- Mouvement Non Uniforme :
Les différences dans les trajectoires peuvent entraîner un mouvement non uniforme des phalanges, affectant la fluidité et la précision du mouvement de la main bionique.
3- Réduction de l'Efficacité :
Les trajectoires inégales peuvent réduire l'efficacité globale du système, entraînant une utilisation d'énergie inutile et un fonctionnement suboptimal.
4- Usure et fragilité des composants de la structure

PARTIE 2: CAHIER DES CHARGES DE LA PROBLEMATQUE MECANIQUE

Intégration de Fusion 360 dans le processus de conception :


La conception de la main bionique s'est réalisée à l'aide du logiciel Fusion 360, offrant ainsi une plateforme collaborative pour la modélisation et la simulation. Cette solution permet d'apporter des modifications précises à la conception, d'effectuer des simulations virtuelles pour évaluer le comportement mécanique, et d'itérer rapidement sur les solutions envisagées.

REMARQUE : Concernant les ajustements mécaniques à entreprendre, ils seront réalisés soit directement sur la plateforme Fusion 360, soit en convertissant les fichiers pour les traiter sur SolidWorks. Le choix entre ces deux méthodes dépendra du temps disponible pour me familiariser avec le logiciel de conception Fusion 360. En cas de contraintes temporelles, l'option privilégiée sera l'utilisation de SolidWorks.

Les raisons possibles pour maintenir les fils parallèles :

Le maintien de parallélisme des fils dans une structure mécanique, telle qu'une main bionique, est important pour plusieurs raisons mécaniques.

1- Distribution uniforme des charges : Lorsque les fils sont parallèles, la charge appliquée est répartie de manière plus uniforme sur l'ensemble des phalanges du doigt. Cela réduit les points de concentration de contrainte, ce qui peut contribuer à prévenir la déformation excessive ou la rupture de composants.

Répartition de la force sur une structure linéaire :

Où :

σ est la contrainte
F est la force appliquée sur le fil
A est la section transversale des composants de la phalange.

2- Réduction des contraintes : Des fils parallèles minimisent les contraintes inutiles sur les composants mécaniques des doigts. Cela peut aider à prolonger la durée de vie des matériaux en évitant des contraintes excessives qui pourraient conduire à la fatigue des matériaux.

Relation entre la contrainte (σ) et la fatigue des matériaux des phalanges :

Où :

Nf est le nombre de cycles de fatigue des matériaux, σlim est la limite de contraintes mécaniques
σ est la contrainte actuelle.

3- Conservation de l'énergie : Lors de l'articulation d'une prothèse, des fils parallèles minimisent les pertes d'énergie dues à la friction et à la résistance. Une trajectoire de mouvement optimisée avec des fils parallèles contribue à une meilleure efficacité mécanique.

Travail (W) effectué par une force constante (F) sur une distance (d) :

W=F⋅d

4- Précision du mouvement : Le parallélisme des fils contribue à maintenir la précision du mouvement de la prothèse. Cela est crucial pour reproduire de manière réaliste la fonctionnalité de la main humaine. Des mouvements précis peuvent faciliter la manipulation d'objets et améliorer l'expérience utilisateur

Erreur de position (εp) due à une force de friction (Ff) :

εp=K*Ff où K est la raideur du système.

5- Stabilité et prévisibilité : le parallélisme des fils favorise la stabilité et la prévisibilité du système. Lorsque les fils suivent des trajectoires parallèles, les mouvements articulaires sont plus stables, réduisant les risques de déviation indésirable ou de comportement erratique.

Moment de torsion (M) nécessaire pour une articulation stable :

M=F⋅d

où

d est la distance entre l'axe de rotation et F la force appliquée.

6- Réduction de l'usure : L'usure des composants mécaniques peut être réduite lorsque les fils restent parallèles. Des trajectoires de mouvement cohérentes minimisent les forces latérales qui pourraient accélérer l'usure des surfaces de contact.

Relation entre la force latérale (latFlat) et l'usure (W) :

W=Flat ⋅d et : d représente la distance sur laquelle la force latérale est appliquée

Solutions mécaniques envisageables à apporter :

1- Optimisation de la trajectoire des fils :
Utilisation de l’outil de modélisation (Fusion360) de modélisation dans Fusion 360 pour ajuster la trajectoire des fils. Assurez-vous que les guides de fil sont conçus de manière à minimiser la déviation pendant l'articulation.

Minimiser les frottements entre les fils et les composants lors du déplacement des fils et garantir une distribution uniforme des forces, favorisant ainsi le parallélisme des fils.

2- Simulation mécanique :

Utilisation des fonctionnalités de simulation de Fusion 360 pour analyser le comportement mécanique de la main bionique en action. Cela pourrait m’aider à identifier les points de déviation et à ajuster la conception en conséquence.

3- Utilisation de mécanismes de guidage supplémentaires :
Ajoutez des mécanismes de guidage supplémentaires pour maintenir le parallélisme des fils. Ces composants peuvent guider les fils tout au long de leur déplacement, minimisant ainsi les déviations, assurant ainsi le maintien du parallélisme.

4- Utilisation de Guides ou de Roulements :
Intégrer des guides ou des roulements pour contrôler et maintenir les trajectoires des fils pendant l’articulation, assurant ainsi le maintien du parallélisme.

5- Analyse des Contraintes Mécaniques :
Utiliser des simulations mécaniques pour analyser comment les contraintes mécaniques influencent les trajectoires et effectuer un ajustement de la conception en conséquence.

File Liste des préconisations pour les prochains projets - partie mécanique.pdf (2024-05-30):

S8 2024

1

## Liste des préconisations pour les prochains projets

Améliorations mécanique :

- Inclure la carte électronique, les servomoteurs et potentiellement une batterie dans le bras.
- Étudier la longueur et le matériau des fils
- Résoudre le problème d’avalement des fils lors du mouvement des doigts
- Avoir un pouce opposable
- Penser à la friction et la fragilité
- Choisir les bons matériaux
- Dimensions proches de la réalité
- Possibilité de montage/démontage pour réparabilité
- Ajouter une interface pour lire des informations
- Créer un autre bras symétrique
- Capteurs de force

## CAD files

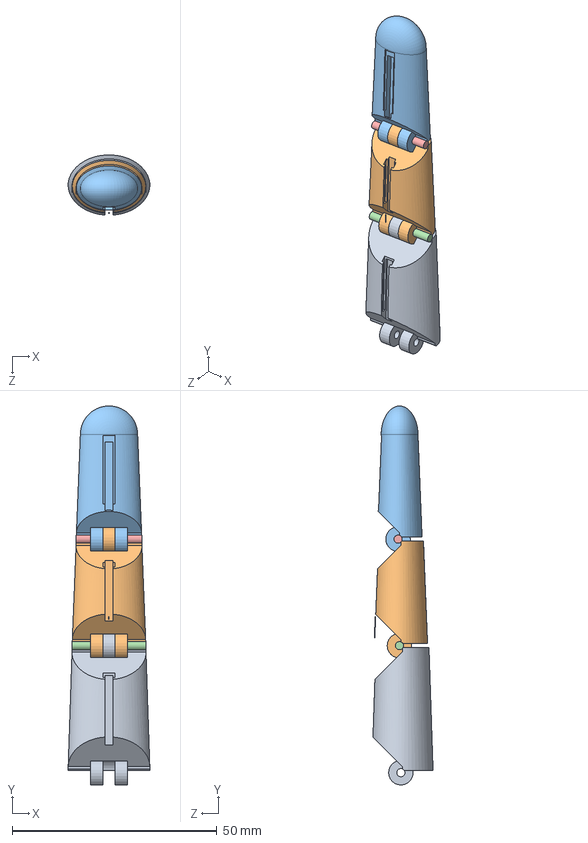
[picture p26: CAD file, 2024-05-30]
Assemblage1.SLDASM
20.0 x 92.5 x 14.7 mm
Pièce1
Pièce2
Pièce3
Mate1
Mate2

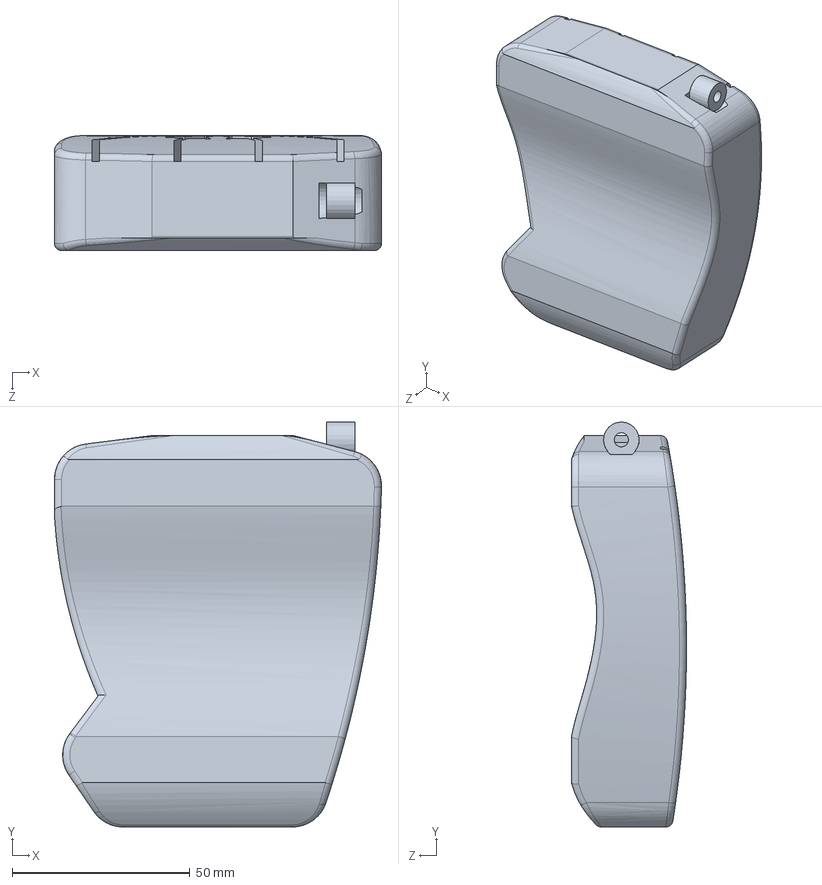
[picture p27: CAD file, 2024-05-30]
main awa.SLDPRT
91.9 x 113.8 x 32.3 mm

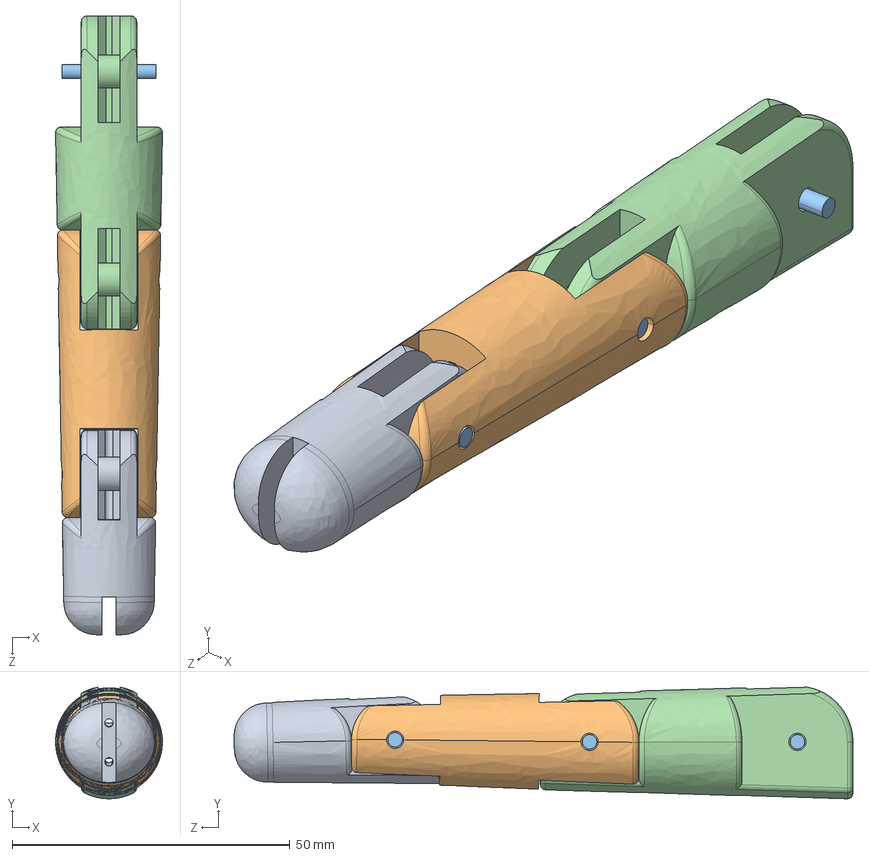
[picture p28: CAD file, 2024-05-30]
Design 1 - Prototype 1/Middle-Finger-Design1.STEP
19.3 x 20.1 x 111.5 mm
Distal_1
intermediate_
Pin-1.1
Pin2-1
Pin3-1
Proximal_1

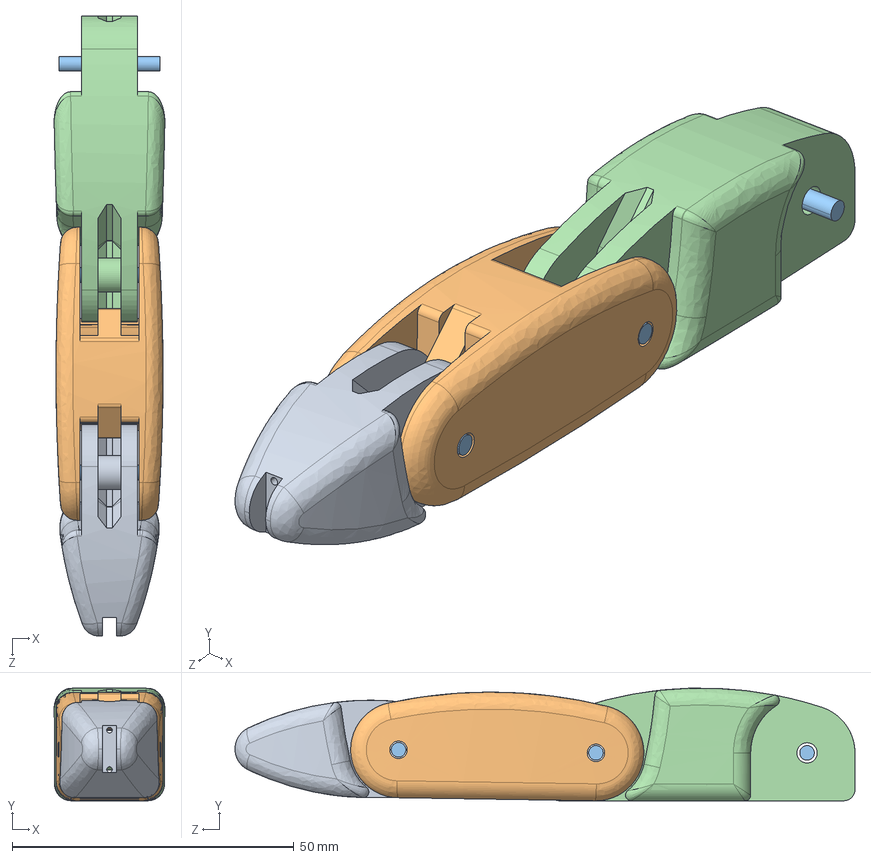
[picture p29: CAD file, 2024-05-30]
Design 2 - Prototype 2/Middle-finger-design-2.STEP
19.6 x 20.0 x 110.0 mm
Distal_phalanges_2
intermedite_Phalanges_2
Pin1-2
Pin2-2
Pin3-2
Proximal_phlanges_2

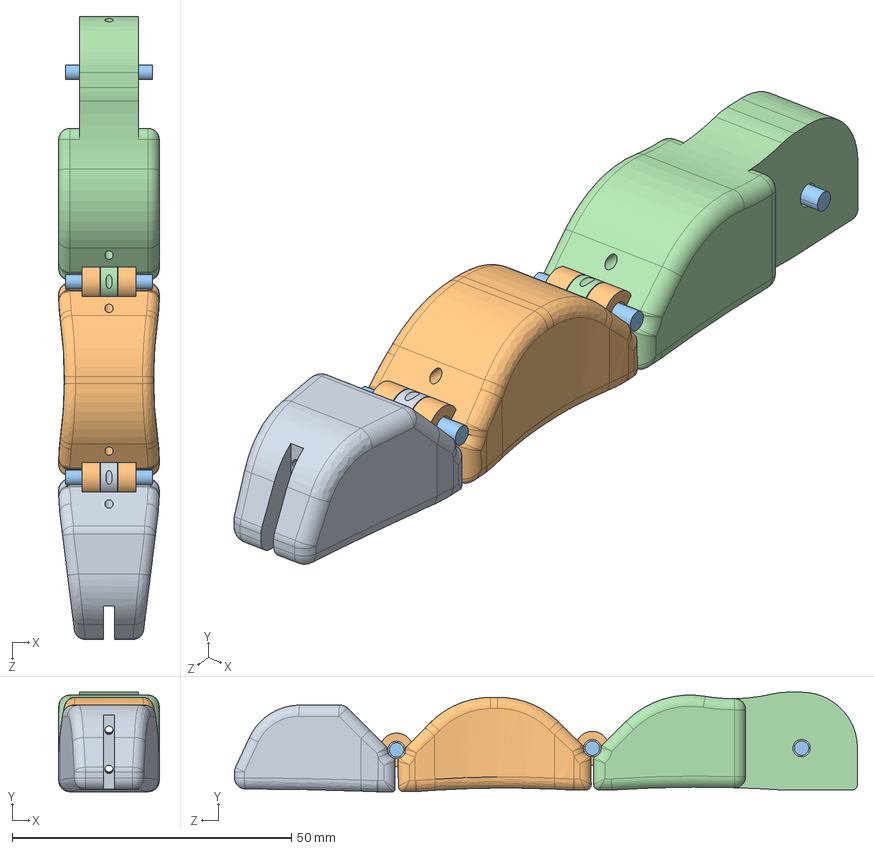
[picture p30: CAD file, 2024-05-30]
Design 3 - Prototype 3/Middle-finger-design-3.STEP
18.0 x 17.8 x 111.5 mm
Distal_Phaanges_3
Intermedite_phalanges_3
Pin_1.3
Pin_2.3 x 2
Proximal_phalanges_3

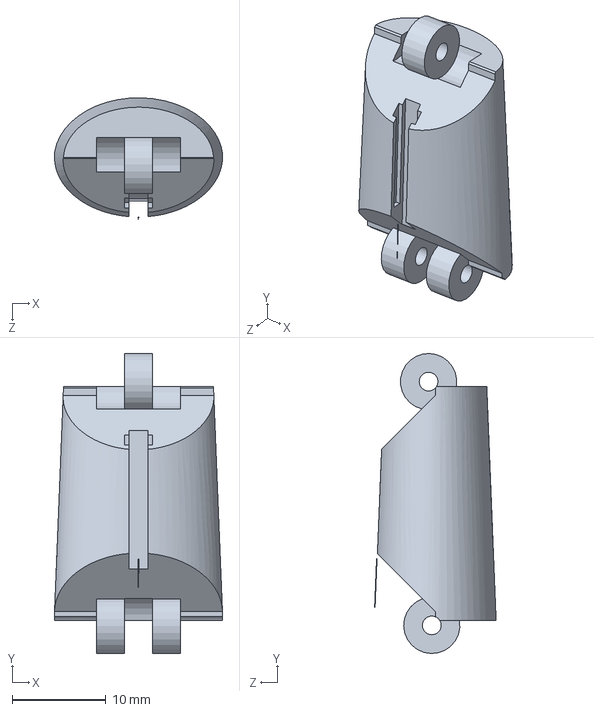
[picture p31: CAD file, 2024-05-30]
ensemble doigts/Pièce2.SLDPRT
18.0 x 32.0 x 12.9 mm

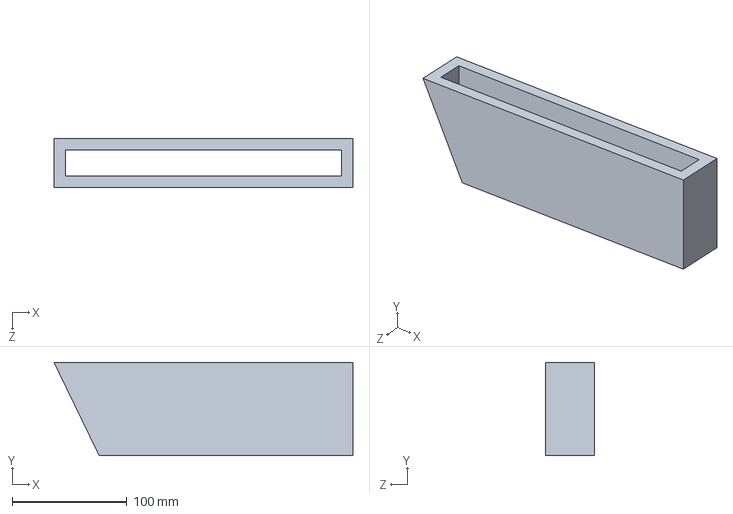
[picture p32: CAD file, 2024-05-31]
essai_bras2_victoria.SLDPRT
260.0 x 81.0 x 43.0 mm

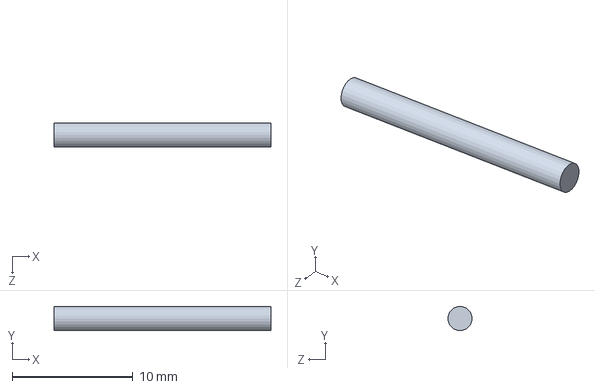
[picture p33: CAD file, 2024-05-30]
ensemble doigts/Mate1.SLDPRT
18.0 x 2.00 x 2.00 mm

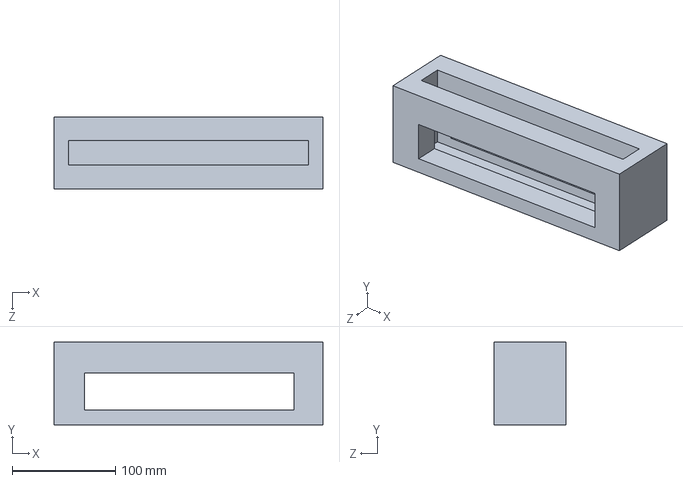
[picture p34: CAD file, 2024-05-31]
essai_bras1_victoria.SLDPRT
260.0 x 80.0 x 70.0 mm

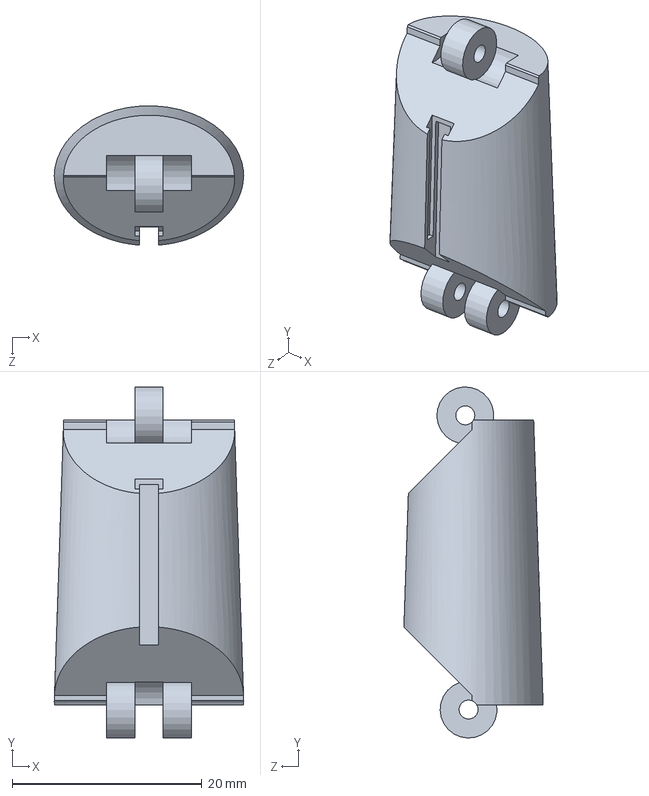
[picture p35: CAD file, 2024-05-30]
ensemble doigts/Pièce1.SLDPRT
20.0 x 37.0 x 14.7 mm

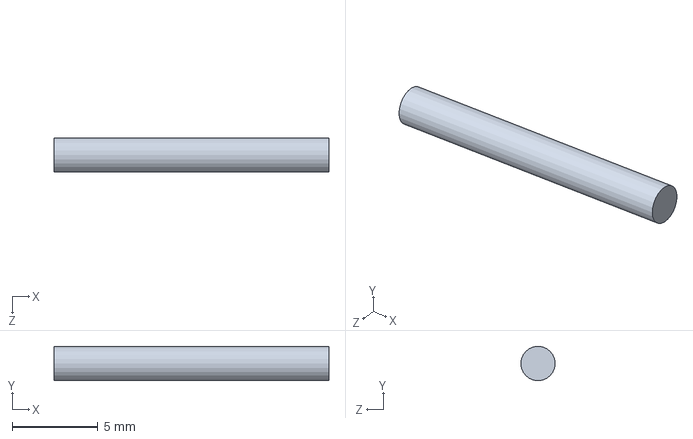
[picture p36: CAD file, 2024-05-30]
ensemble doigts/Mate2.SLDPRT
16.0 x 2.00 x 2.00 mm

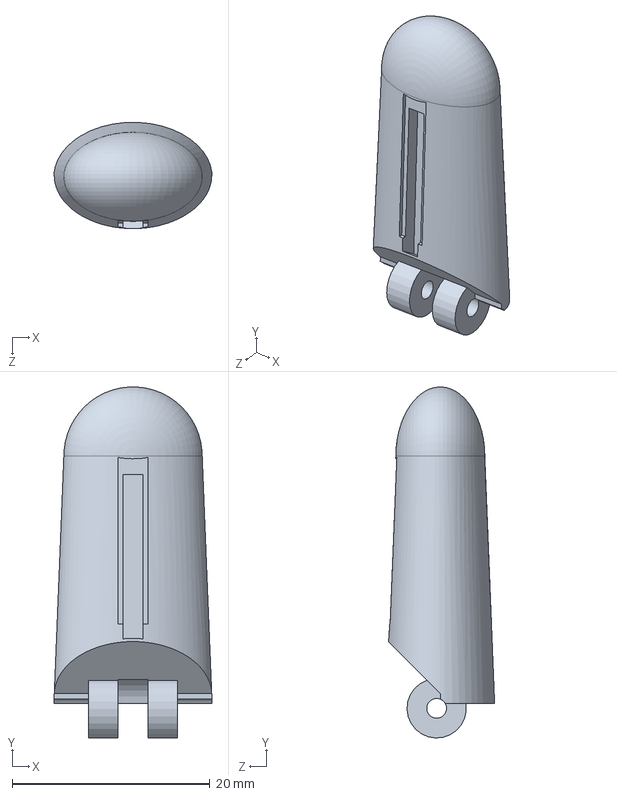
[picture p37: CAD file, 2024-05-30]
ensemble doigts/Pièce3.SLDPRT
16.0 x 35.5 x 10.7 mm
